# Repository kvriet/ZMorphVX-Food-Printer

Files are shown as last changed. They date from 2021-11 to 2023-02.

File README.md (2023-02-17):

This is a student repository created for the ZMorphVX Printer with Thick Paste Extruder, owned by the TU/e (Eindhoven University of Technology).

Here you can find:
- A folder with STLs of luer lock nozzles. We've achieved good results with FDM printing these nozzles at 0.1mm layer height. Resin printing could also be an option. Please bear in mind that 3D-printed nozzles will not be food safe!
- A ZMorphVX Thick Paste Cura Profile. With this profile we obtained good flow results with a 2mm nozzle and vegan (aqua faba) meringue mixture. Baking these prints in the oven produced disappointing results. We obtained better results with meringue prints from egg (non-vegan).
- A logbook with our lab notes where we describe what we tried in terms of printing material, geometries (infill settings) and printer settings.

About the Cura profiles:
- We sometimes observed problems importing the profiles into newer versions of Cura. These profiles were created in Cura 4.6.
- If the Cura profile doesn't load correctly, these are the main things to try to adjust:
* speed (10 to 20 mm/s seems to work well)
* flow (between 5 and 15%)
* line width and layer height roughly the same, and should be your nozzle size
* No spiralise outer contour

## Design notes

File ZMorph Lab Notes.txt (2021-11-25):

Lab notes for developing a paste for 3D printing and exploring different printing geometries and techniques
by Katrien van Riet

Meringue printing #1 - 9/11/2021

Objective: get a feel for the printer with an existing food 3D printing recipe.

Results: We didn't manage to print anything due to missing parts / nozzles that were too short.

Problems:
- nozzle approx. 14mm too short
- (syringe doesn't go into x carriage deep enough)

Solutions:
- (resin) print new nozzles to fit luer lock syringe
- extend current nozzle
- buy longer nozzles

Meringue printing #2 - 15/11/2021

Objective: get a feel for the printer with a vegan 3D food printing recipe

Done since last time:
- FDM printed a number of nozzles in PLA (0.1 layer height): 0.75, 1, 1.5, 2, 3mm

Results: 
Mixture #1: 
Ingredients aqua faba (didn't weigh but probably 150 gr) + 250gr sugar + 1/2 tsp cream of tartar. 20 mins of whipping: still not firm enough for printing in height. Much less firm than egg white meringue.

Mixture #2:
Added 1 packet of klopfix to remainder (1/2?) of the mixture but still too soft
We used a creme brulee burner to bake the meringues a little which helped them retain their shape.

Meringue printing #3 - 17/11/2021

Objectives: make a firmer vegan meringue mixture and print with it

Results:
Mixture #1:
- 94 gr aqua faba
- 47 gr sugar
- 141 gr sugar
- 47 gr water
- 1.3 gr cream of tartar

This meringue is much more firm! First succesful print!

Cura profile:
- initial layer height: 0.5mm
- lower layer: 2mm
- initial flow: 15%
- normal flow: 5%

We need to keep track of the total volume of what we want to print as our syringe volume is roughly 70ml.

Meringue printing #4 - 18/11/2021

Objectives: add agar to the meringue mixture and test with print

Results:
Mixture #1:
- 104 gr aqua faba
- 52 gr water
- 158 gr sugar
- 52 gr water
- 1.3 gr cream of tartar
- 0.8 gr agar

Printed a hollow cylinder without bottom. Was quite firm but showed buckling at the base. Printed bar held up quite well but started showing buckling on infill at roughly layer 5. Top infill worked well.

Meringue printing #5 - 24/11/2021

Objectives: add chlorella to the meringue mixture and test with print
try different geometries and print settings to create higher resolution
try baking the prints in the oven straight away

Results
Mixture #1:
- 92 gr aqua faba
- 46 gr sugar
Whip until stiff

- 46 gr water
- 138 gr water
- 1.3 gr cream of tartar
Boil to 120 degrees C

Add hot sugar mix to aqua faba whip

Add
- 1.38 gr agar to the warm mix

Add
- 1.3 gr chlorella to the mix

The meringue did not become stiff/firm. We think this was vecause 20 mins elapsed between whipping the aqua faba and adding the sugar water.

Mixture #2:
- 96 gr aqua faba
- 48 gr sugar
Whip until stiff

- 48 gr water
- 144 gr water
- 1.3 gr cream of tartar
Boil to 120 degrees C

Add hot sugar mix to aqua faba whip

Add
- 0.96 gr agar to the warm mix (1% of aqua faba amount)

Add
- 3.8 gr chlorella to the mix (1% of total mixture (minus chlorella) amount)

The meringue was firmer than the mixture without chlorella (18/11/2021). Possibly adding the chlorella enabled the colloid function of the small chlorella particles.

Baked all of them in the oven at 100 degrees Celsius for 30-45 mins. 

Finding:
With a 15% lines infill, we could see the infill through the top layer of the baked meringue. This is an interesting effect that we can possibly leverage in future designs. Most of the bars looked like rectangular blobs after baking. 

Future steps/things to check:
Maybe increase heat a little (130?) to make the meringue set more quickly, thus reducing sag and maintaining the printed shape better. We could also place an oven thermometer inside the oven to check if it really heats up to 100 degrees. Also, we placed the bars directly on to the metal plate at the bottom of the oven. A raised platform (with a finer mesh to prevent meringue from sagging through) might work better. Now the bottom of the bars got burnt because of the hot metal sheet. Maybe we can use the foaminess of the meringue batter as an asset/feature in our designs?

New profile created for 1mm nozzles.

The following settings seem to work well:
- 2mm layer height
- 1mm nozzle 
- flow rate: 5% for lines, or 10% for tri-hex (always 15% initial layer)
- speed 5 mm/s
- infill: 10% lines or 15% tri-hex
- no bottom
- experiment with no top

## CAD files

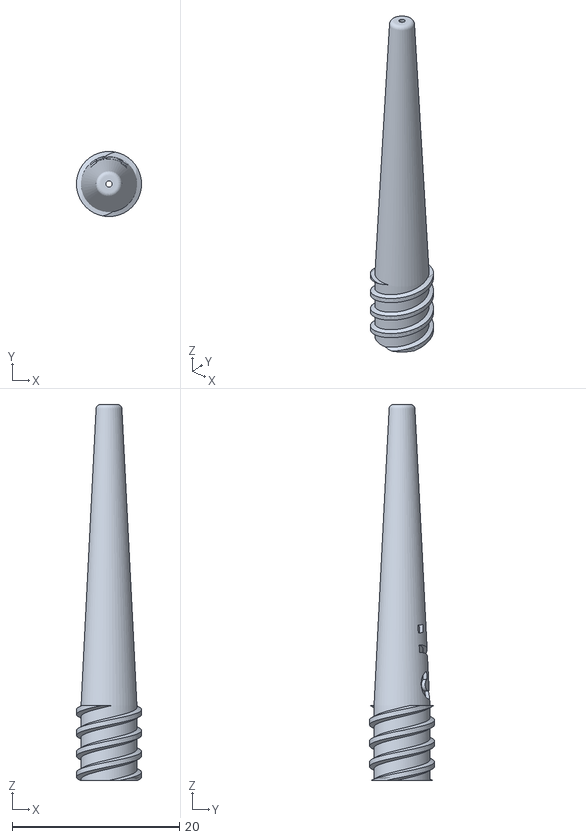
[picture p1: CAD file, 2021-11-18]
Luer Lock Nozzles/luer lock nozzle 0.75mm 4.4mm ID emboss.stl
7.79 x 7.79 x 45.0

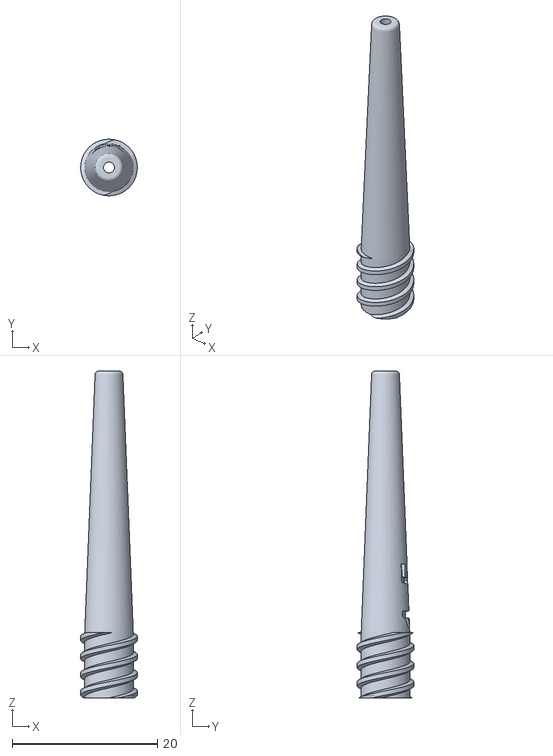
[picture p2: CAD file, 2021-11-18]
Luer Lock Nozzles/luer lock nozzle 1.5mm 4.4mm ID emboss.stl
7.79 x 7.79 x 45.0

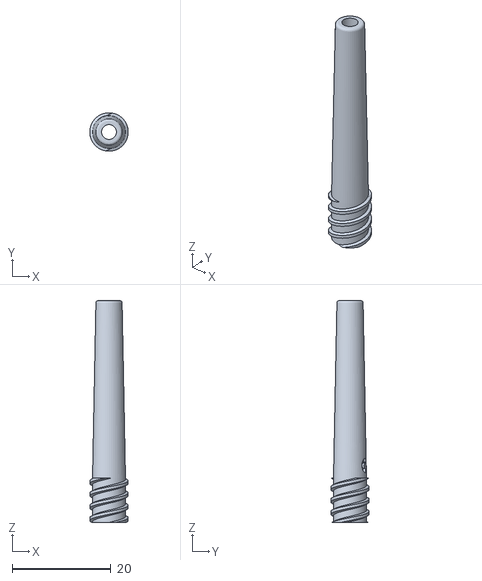
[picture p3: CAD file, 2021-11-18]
Luer Lock Nozzles/luer lock nozzle 3mm 4.4mm ID emboss.stl
7.79 x 7.79 x 45.0

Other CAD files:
Luer Lock Nozzles/luer lock nozzle 1mm 4.4mm ID emboss.stl
Luer Lock Nozzles/luer lock nozzle 2mm 4.4mm ID emboss.stl

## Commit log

2021-11-18 Uploaded luer lock and cura profile
    [luer lock nozzle 0.75mm 4.4mm ID emboss.stl, luer lock nozzle 1.5mm 4.4mm ID emboss.stl, luer lock nozzle 1mm 4.4mm ID emboss.stl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]
2021-11-25 1mm profile added, updated log book
